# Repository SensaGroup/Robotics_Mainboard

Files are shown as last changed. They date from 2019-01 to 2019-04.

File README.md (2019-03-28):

# SENSA - Robotics_Mainboard

SENSA Mainboard is used on the Eurobot 2019 competition.

## Description
The Mainboard is the commander of the robot system. 
We used an Arduino Mega for the base and we developed the extension board

## Features
- 5V/12V inputs with protection
- 4x servo pinouts with external 5V power supply
- 6x 12V pneumatic valve controller
- 2x high-current relays 
- AX-12 support
- 6x optoisolated 12V infrared sensor inputs
- 6x binary 5V sensor inputs
- CAN-Bus (MCP25625)
- NRF24L01
- HC-05 Bluetooth pinout
- I2C/UART pinouts

## Software
All software is written in C for AVR.
View README in the Software folder.

## Pictures
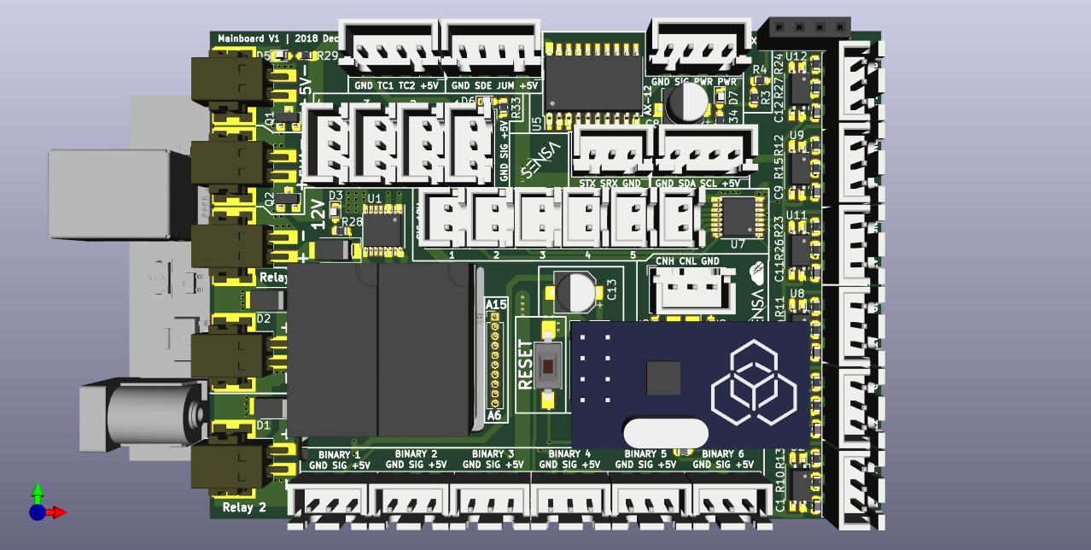
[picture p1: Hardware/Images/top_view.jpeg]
Top_view


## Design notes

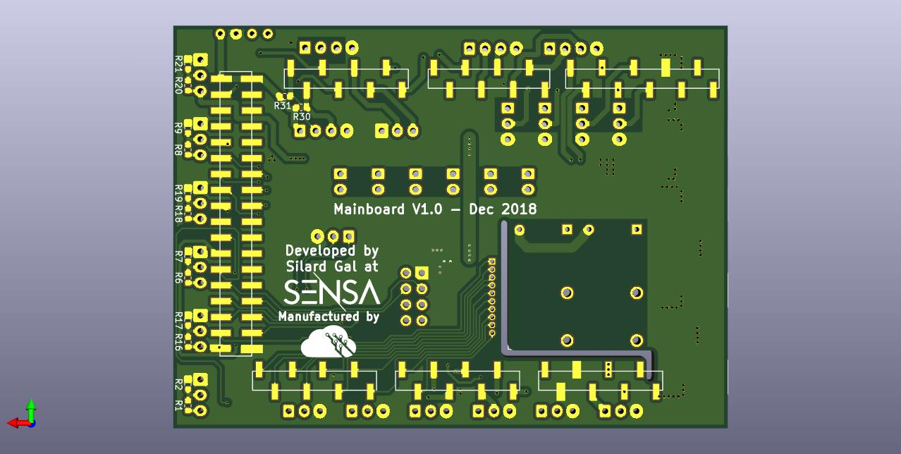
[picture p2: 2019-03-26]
Hardware/Images/bottom_view.jpeg

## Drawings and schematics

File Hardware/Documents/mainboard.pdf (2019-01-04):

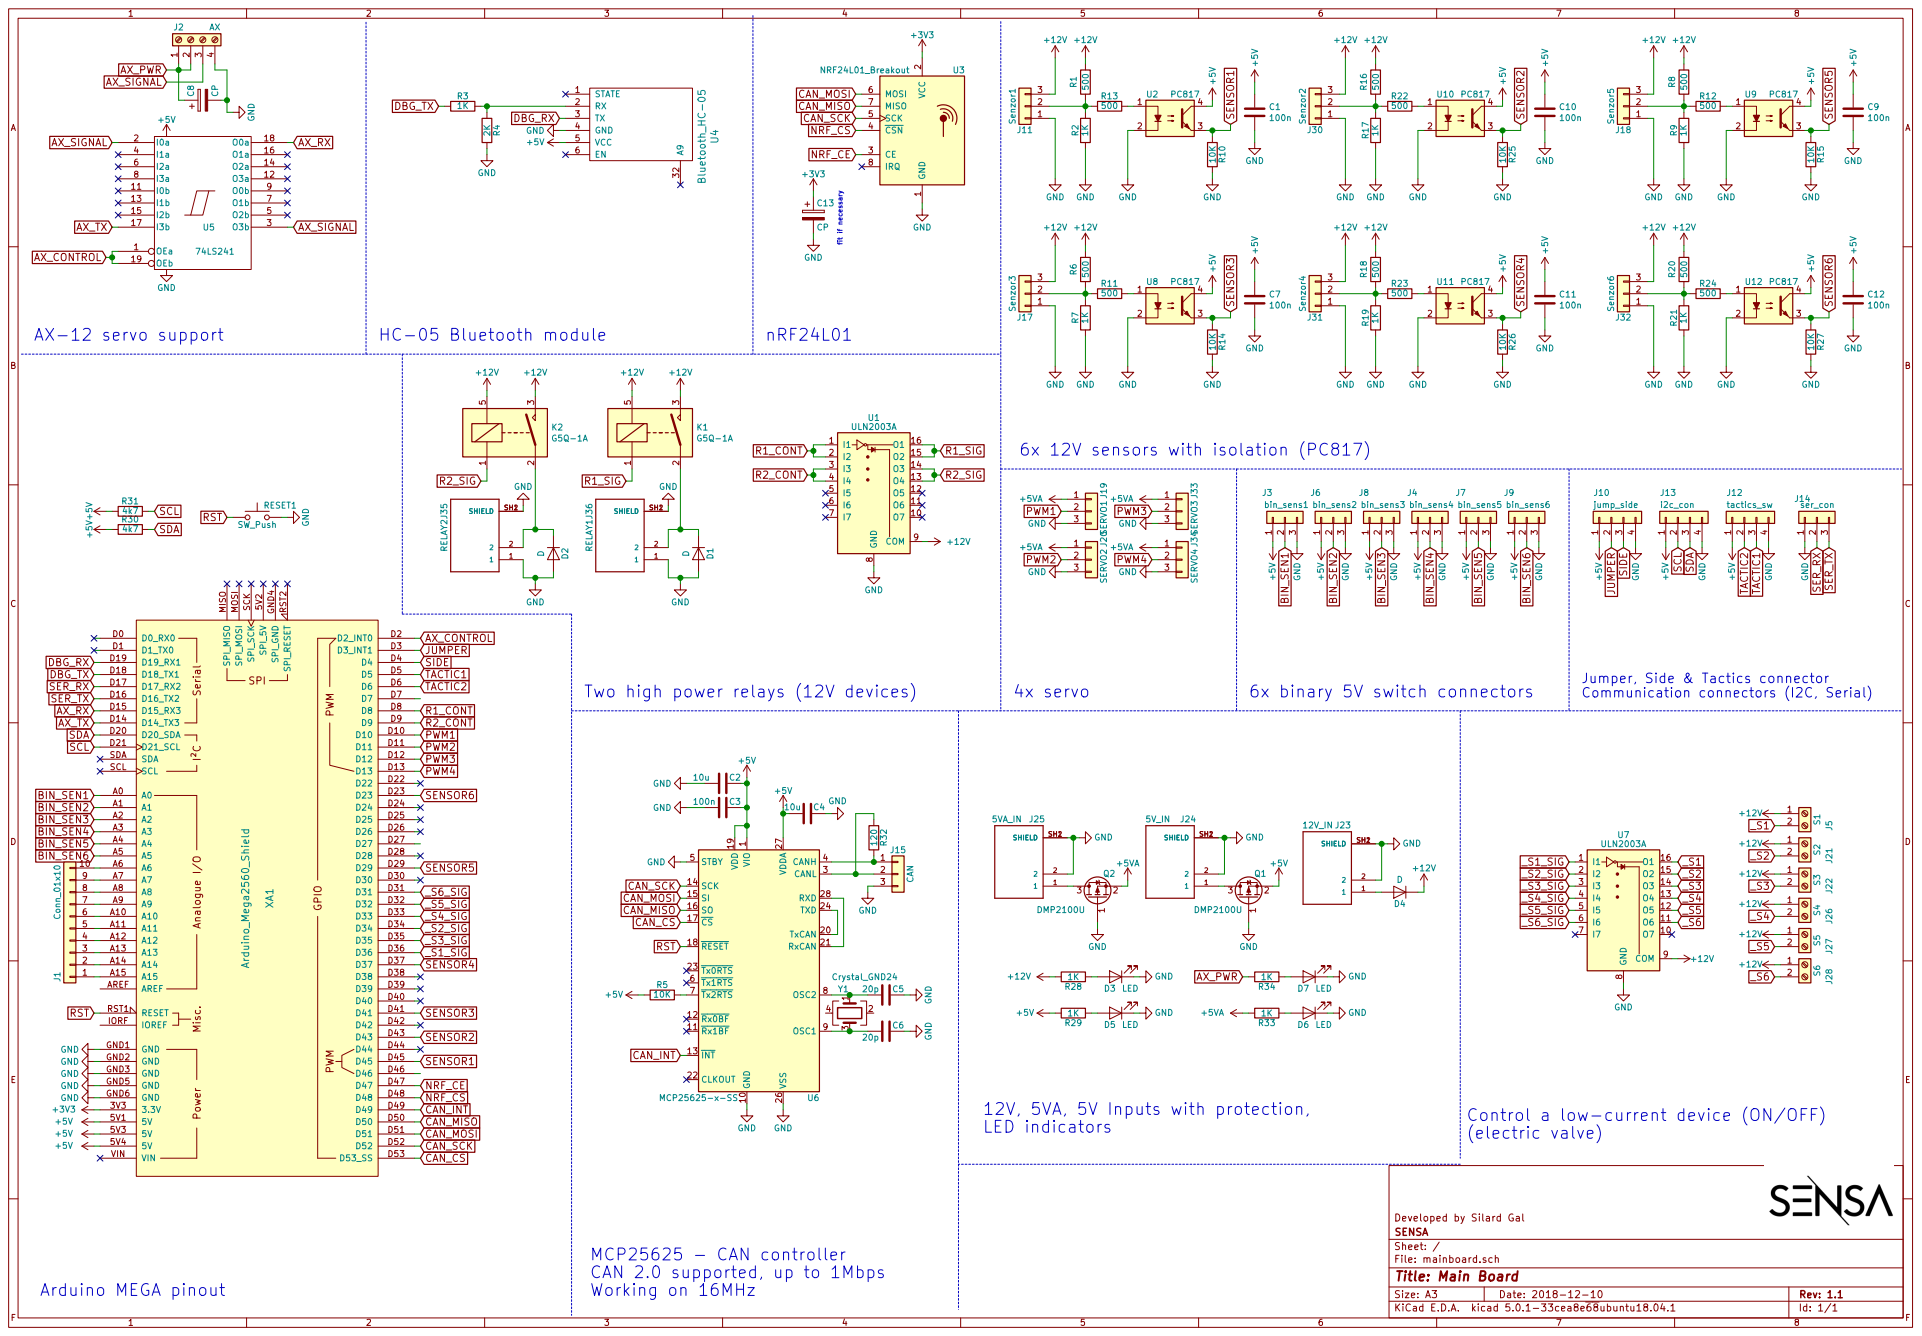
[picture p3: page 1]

2 CE 3 CSN 4 SCK 5 MOSI 6 MISO 7

Jumper, Side & Tactics connector
Communication connectors (I2C, Serial)

GND GND GND GND GND

Control a low-current device (ON/OFF)
(electric valve)

File: mainboard.sch Sheet: / SENSA

MCP25625 - CAN controller
CAN 2.0 supported, up to 1Mbps

Id: 1/1 Title: Main Board

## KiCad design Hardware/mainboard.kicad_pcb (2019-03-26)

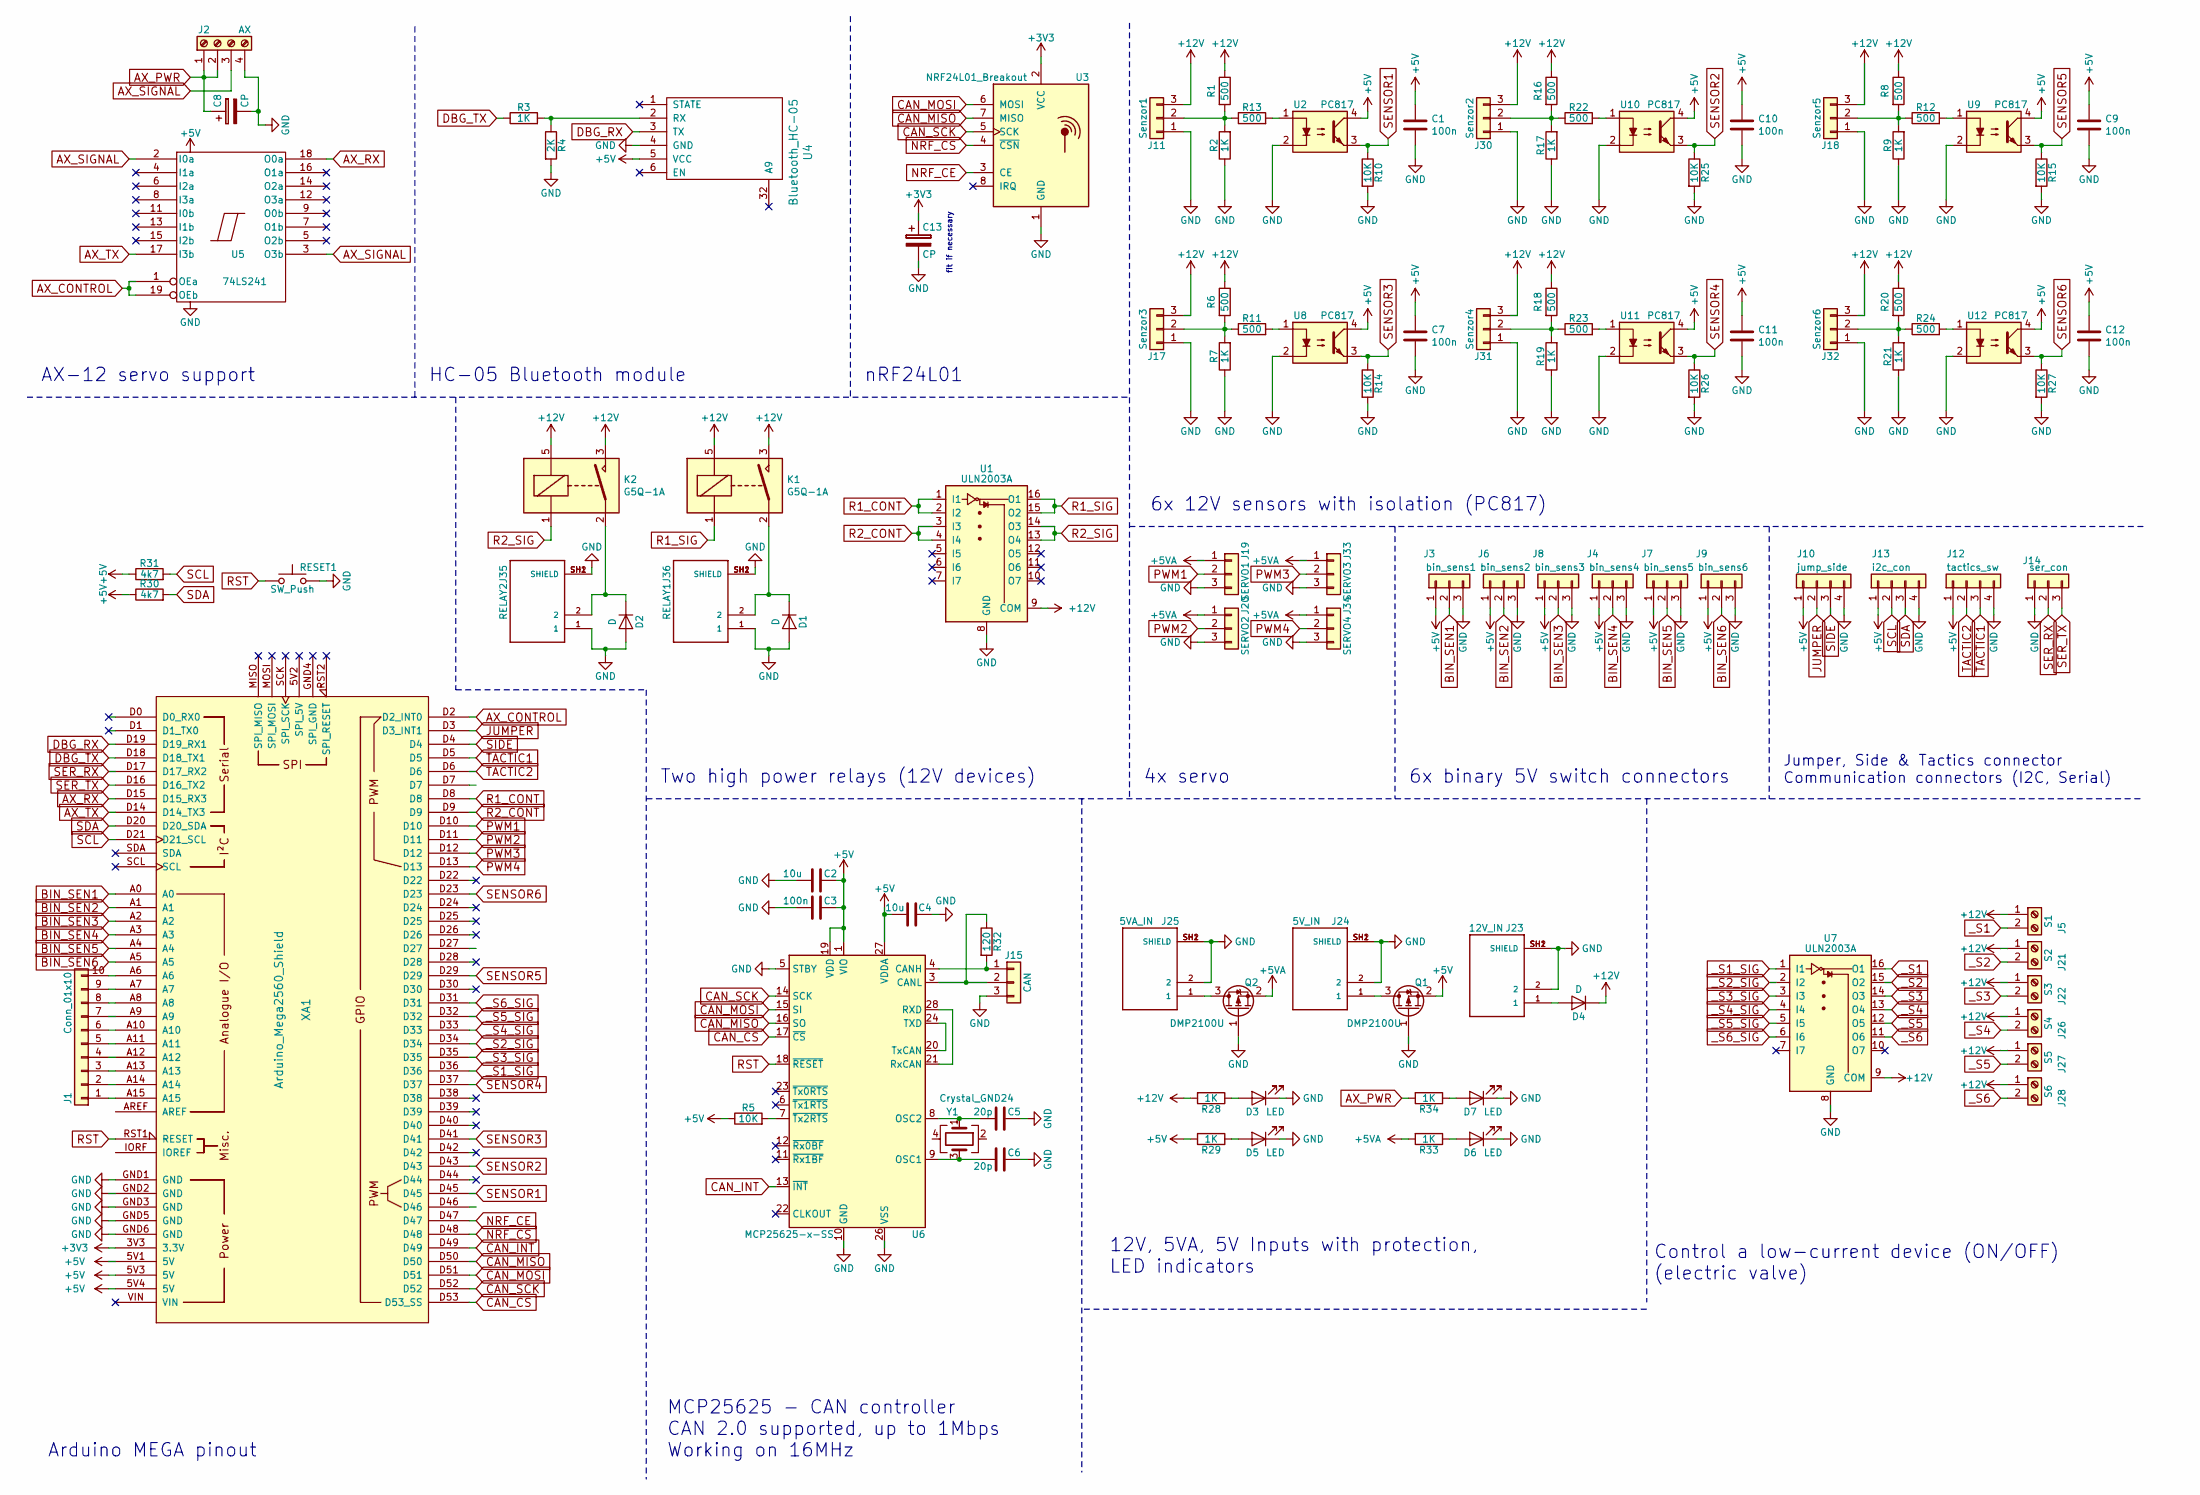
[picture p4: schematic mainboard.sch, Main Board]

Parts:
C1, C3, C7, C9, C10, C11, C12: 100n; C_0603_1608Metric
C2, C4: 10u; C_0603_1608Metric
C5, C6: 20p; C_0603_1608Metric
C8, C13: CP; CP_Elec_5x5.8
D1, D2, D4: D; D_SMA
D3, D5, D6, D7: LED; LED_0603_1608Metric
J1: Conn_01x10; PinHeader_1x10_P1.27mm_Vertical
J2: AX; JST_XH_B04B-XH-A_1x04_P2.50mm_Vertical
J3: bin_sens1; JST_XH_B03B-XH-A_1x03_P2.50mm_Vertical
J4: bin_sens4; JST_XH_B03B-XH-A_1x03_P2.50mm_Vertical
J5: S1; JST_XH_B02B-XH-A_1x02_P2.50mm_Vertical
J6: bin_sens2; JST_XH_B03B-XH-A_1x03_P2.50mm_Vertical
J7: bin_sens5; JST_XH_B03B-XH-A_1x03_P2.50mm_Vertical
J8: bin_sens3; JST_XH_B03B-XH-A_1x03_P2.50mm_Vertical
J9: bin_sens6; JST_XH_B03B-XH-A_1x03_P2.50mm_Vertical
J10: jump_side; JST_XH_B04B-XH-A_1x04_P2.50mm_Vertical
J11: Senzor1; JST_XH_B03B-XH-A_1x03_P2.50mm_Vertical
J12: tactics_sw; JST_XH_B04B-XH-A_1x04_P2.50mm_Vertical
J13: i2c_con; JST_XH_B04B-XH-A_1x04_P2.50mm_Vertical
J14: ser_con; JST_XH_B03B-XH-A_1x03_P2.50mm_Vertical
J15: CAN; JST_XH_B03B-XH-A_1x03_P2.50mm_Vertical
J17: Senzor3; JST_XH_B03B-XH-A_1x03_P2.50mm_Vertical
J18: Senzor5; JST_XH_B03B-XH-A_1x03_P2.50mm_Vertical
J19: SERVO1; JST_XH_B03B-XH-A_1x03_P2.50mm_Vertical
J20: SERVO2; JST_XH_B03B-XH-A_1x03_P2.50mm_Vertical
J21: S2; JST_XH_B02B-XH-A_1x02_P2.50mm_Vertical
J22: S3; JST_XH_B02B-XH-A_1x02_P2.50mm_Vertical
J23: 12V_IN; PHOENIX_1702473
J24: 5V_IN; PHOENIX_1702473
J25: 5VA_IN; PHOENIX_1702473
J26: S4; JST_XH_B02B-XH-A_1x02_P2.50mm_Vertical
J27: S5; JST_XH_B02B-XH-A_1x02_P2.50mm_Vertical
J28: S6; JST_XH_B02B-XH-A_1x02_P2.50mm_Vertical
J30: Senzor2; JST_XH_B03B-XH-A_1x03_P2.50mm_Vertical
J31: Senzor4; JST_XH_B03B-XH-A_1x03_P2.50mm_Vertical
J32: Senzor6; JST_XH_B03B-XH-A_1x03_P2.50mm_Vertical
J33: SERVO3; JST_XH_B03B-XH-A_1x03_P2.50mm_Vertical
J34: SERVO4; JST_XH_B03B-XH-A_1x03_P2.50mm_Vertical
J35: RELAY2; PHOENIX_1702473
J36: RELAY1; PHOENIX_1702473
K1, K2: G5Q-1A; Relay_SPST_Omron-G5Q-1A
Q1, Q2: DMP2100U; SOT-23
R1, R6, R8, R11, R12, R13, R16, R18, R20, R22, R23, R24: 500; R_0603_1608Metric
R2, R3, R7, R9, R17, R19, R21, R28, R29, R33, R34: 1K; R_0603_1608Metric
R4: 2K; R_0603_1608Metric
R5, R10, R14, R15, R25, R26, R27: 10K; R_0603_1608Metric
R30, R31: 4k7; R_0603_1608Metric
R32: 120; R_0603_1608Metric
RESET1: SW_Push; SW_SPST_FSMSM
U1, U7: ULN2003A; TSSOP-16-1EP_4.4x5mm_P0.65mm
U2, U8, U9, U10, U11, U12: PC817; SOP-4_4.4x2.8mm_P1.27mm
U3: NRF24L01_Breakout; PinHeader_2x04_P2.54mm_Vertical
U4: Bluetooth_HC-05
U5: 74LS241; SOIC-20W_7.5x12.8mm_P1.27mm
U6: MCP25625-x-SS; SSOP-28_5.3x10.2mm_P0.65mm
XA1: Arduino_Mega2560_Shield
Y1: Crystal_GND24; Crystal_SMD_SeikoEpson_FA238V-4Pin_3.2x2.5mm_HandSoldering

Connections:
+3V3: C13.1, U3.2 (VCC), XA1.3V3 (3.3V); also elsewhere on the board
+5V: C1.1, C2.1, C3.1, C4.1, C7.1, C9.1, C10.1, C11.1, C12.1, J3.1, J4.1, J6.1, J7.1, J8.1, J9.1, J10.1, J12.1, J13.1, Q1.2 (S), R5.1, R29.2, R30.1, R31.1, U2.4, U4.5 (VCC), U5.20 (VCC), U6.1 (VIO), U6.19 (VDD), U6.27 (VDDA), U8.4, U9.4, U10.4, U11.4, U12.4, XA1.5V1 (5V), XA1.5V3 (5V), XA1.5V4 (5V); also elsewhere on the board
+5VA: J19.1, J20.1, J33.1, J34.1, Q2.2 (S), R33.2
+12V: D4.1 (K), J5.1, J11.3, J17.3, J18.3, J21.1, J22.1, J26.1, J27.1, J28.1, J30.3, J31.3, J32.3, K1.3, K1.5, K2.3, K2.5, R1.1, R6.1, R8.1, R16.1, R18.1, R20.1, R28.2, U1.9 (COM), U7.9 (COM)
AX_CONTROL: U5.1 (OEa), U5.19 (OEb), XA1.D2 (D2_INT0); also elsewhere on the board
AX_PWR: C8.1, J2.1, J2.2, R34.2
AX_RX: U5.18 (O0a), XA1.D15 (D15_RX3); also elsewhere on the board
AX_SIGNAL: J2.3, U5.2 (I0a), U5.3 (O3b)
AX_TX: U5.17 (I3b), XA1.D14 (D14_TX3); also elsewhere on the board
BIN_SEN1: J3.2, XA1.A0; also elsewhere on the board
BIN_SEN2: J6.2, XA1.A1; also elsewhere on the board
BIN_SEN3: J8.2, XA1.A2; also elsewhere on the board
BIN_SEN4: J4.2, XA1.A3; also elsewhere on the board
BIN_SEN5: J7.2, XA1.A4; also elsewhere on the board
BIN_SEN6: J9.2, XA1.A5; also elsewhere on the board
CAN_CS: U6.17 (~CS), XA1.D53 (D53_SS); also elsewhere on the board
CAN_INT: U6.13 (~INT), XA1.D49; also elsewhere on the board
CAN_MISO: U3.7 (MISO), U6.16 (SO), XA1.D50; also elsewhere on the board
CAN_MOSI: U3.6 (MOSI), U6.15 (SI), XA1.D51; also elsewhere on the board
CAN_SCK: U3.5 (SCK), U6.14 (SCK), XA1.D52; also elsewhere on the board
DBG_RX: U4.3 (TX), XA1.D19 (D19_RX1); also elsewhere on the board
DBG_TX: R3.1, XA1.D18 (D18_TX1); also elsewhere on the board
GND: C1.2, C2.2, C3.2, C4.2, C5.1, C6.1, C7.2, C8.2, C9.2, C10.2, C11.2, C12.2, C13.2, D1.2 (A), D2.2 (A), D3.1 (K), D5.1 (K), D6.1 (K), D7.1 (K), J2.4, J3.3, J4.3, J6.3, J7.3, J8.3, J9.3, J10.4, J11.1, J12.4, J13.4, J14.1, J15.3, J17.1, J18.1, J19.3, J20.3, J23.2, J23.SH1 (SHIELD), J23.SH2 (SHIELD), J24.2, J24.SH1 (SHIELD), J24.SH2 (SHIELD), J25.2, J25.SH1 (SHIELD), J25.SH2 (SHIELD), J30.1, J31.1, J32.1, J33.3, J34.3, J35.1, J35.SH1 (SHIELD), J35.SH2 (SHIELD), J36.1, J36.SH1 (SHIELD), J36.SH2 (SHIELD), Q1.1 (G), Q2.1 (G), R2.1, R4.2, R7.1, R9.1, R10.2, R14.2, R15.2, R17.1, R19.1, R21.1, R25.2, R26.2, R27.2, RESET1.2, U1.8 (GND), U2.2, U3.1 (GND), U4.4 (GND), U5.10 (GND), U6.5 (STBY), U6.10 (GND), U6.26 (VSS), U7.8 (GND), U8.2, U9.2, U10.2, U11.2, U12.2, XA1.GND1 (GND), XA1.GND2 (GND), XA1.GND3 (GND), XA1.GND5 (GND), XA1.GND6 (GND); also elsewhere on the board
JUMPER: J10.2, XA1.D3 (D3_INT1); also elsewhere on the board
NRF_CE: U3.3 (CE), XA1.D47; also elsewhere on the board
NRF_CS: U3.4 (~CSN), XA1.D48; also elsewhere on the board
unnamed: C5.2, U6.8 (OSC2), Y1.1
unnamed: C6.2, U6.9 (OSC1), Y1.3
unnamed: D1.1 (K), J36.2, K1.2
unnamed: D2.1 (K), J35.2, K2.2
unnamed: D3.2 (A), R28.1
unnamed: D4.2 (A), J23.1
unnamed: D5.2 (A), R29.1
unnamed: D6.2 (A), R33.1
unnamed: D7.2 (A), R34.1
unnamed 35: J1.1, XA1.A15; also elsewhere on the board
unnamed 36: J1.2, XA1.A14; also elsewhere on the board
unnamed 37: J1.3, XA1.A13; also elsewhere on the board
unnamed 38: J1.4, XA1.A12; also elsewhere on the board
unnamed 39: J1.5, XA1.A11; also elsewhere on the board
unnamed 40: J1.6, XA1.A10; also elsewhere on the board
unnamed 41: J1.7, XA1.A9; also elsewhere on the board
unnamed 42: J1.8, XA1.A8; also elsewhere on the board
unnamed 43: J1.9, XA1.A7; also elsewhere on the board
unnamed 44: J1.10, XA1.A6; also elsewhere on the board
unnamed: J11.2, R1.2, R2.2, R13.1
unnamed: J15.1, R32.2, U6.4 (CANH)
unnamed: J15.2, R32.1, U6.3 (CANL)
unnamed: J17.2, R6.2, R7.2, R11.1
unnamed: J18.2, R8.2, R9.2, R12.1
unnamed: J24.1, Q1.3 (D)
unnamed: J25.1, Q2.3 (D)
unnamed: J30.2, R16.2, R17.2, R22.1
unnamed: J31.2, R18.2, R19.2, R23.1
unnamed: J32.2, R20.2, R21.2, R24.1
unnamed: R3.2, R4.1, U4.2 (RX)
unnamed: R5.2, U6.7 (~Tx2RTS)
unnamed: R11.2, U8.1
unnamed: R12.2, U9.1
unnamed: R13.2, U2.1
unnamed: R22.2, U10.1
unnamed: R23.2, U11.1
unnamed: R24.2, U12.1
unnamed: U6.20 (TxCAN), U6.24 (TXD)
unnamed: U6.21 (RxCAN), U6.28 (RXD)
unnamed 93: XA1.AREF; also elsewhere on the board
unnamed 94: XA1.D0 (D0_RX0); also elsewhere on the board
unnamed 95: XA1.D1 (D1_TX0); also elsewhere on the board
unnamed 96: XA1.D7; also elsewhere on the board
unnamed 97: XA1.D22; also elsewhere on the board
unnamed 98: XA1.D24; also elsewhere on the board
unnamed 99: XA1.D25; also elsewhere on the board
unnamed 100: XA1.D26; also elsewhere on the board
unnamed 101: XA1.D27; also elsewhere on the board
unnamed 102: XA1.D28; also elsewhere on the board
unnamed 103: XA1.D30; also elsewhere on the board
unnamed 104: XA1.D38; also elsewhere on the board
unnamed 105: XA1.D39; also elsewhere on the board
unnamed 106: XA1.D40; also elsewhere on the board
unnamed 107: XA1.D42; also elsewhere on the board
unnamed 108: XA1.D44; also elsewhere on the board
unnamed 109: XA1.D46; also elsewhere on the board
unnamed 110: XA1.IORF (IOREF); also elsewhere on the board
unnamed 111: XA1.SCL; also elsewhere on the board
unnamed 112: XA1.SDA; also elsewhere on the board
unnamed 113: XA1.VIN; also elsewhere on the board
PWM1: J19.2, XA1.D10; also elsewhere on the board
PWM2: J20.2, XA1.D11; also elsewhere on the board
PWM3: J33.2, XA1.D12; also elsewhere on the board
PWM4: J34.2, XA1.D13; also elsewhere on the board
R1_CONT: U1.1 (I1), U1.2 (I2), XA1.D8; also elsewhere on the board
R1_SIG: K1.1, U1.15 (O2), U1.16 (O1)
R2_CONT: U1.3 (I3), U1.4 (I4), XA1.D9; also elsewhere on the board
R2_SIG: K2.1, U1.13 (O4), U1.14 (O3)
RST: RESET1.1, U6.18 (~RESET), XA1.RST1 (RESET); also elsewhere on the board
SCL: J13.2, R31.2, XA1.D21 (D21_SCL); also elsewhere on the board
SDA: J13.3, R30.2, XA1.D20 (D20_SDA); also elsewhere on the board
SENSOR1: R10.1, U2.3, XA1.D45; also elsewhere on the board
SENSOR2: R25.1, U10.3, XA1.D43; also elsewhere on the board
SENSOR3: R14.1, U8.3, XA1.D41; also elsewhere on the board
SENSOR4: R26.1, U11.3, XA1.D37; also elsewhere on the board
SENSOR5: R15.1, U9.3, XA1.D29; also elsewhere on the board
SENSOR6: R27.1, U12.3, XA1.D23; also elsewhere on the board
SER_RX: J14.2, XA1.D17 (D17_RX2); also elsewhere on the board
SER_TX: J14.3, XA1.D16 (D16_TX2); also elsewhere on the board
SIDE: J10.3, XA1.D4; also elsewhere on the board
TACTIC1: J12.3, XA1.D5; also elsewhere on the board
TACTIC2: J12.2, XA1.D6; also elsewhere on the board
_S1: J5.2, U7.16 (O1)
_S1_SIG: U7.1 (I1), XA1.D36; also elsewhere on the board
_S2: J21.2, U7.15 (O2)
_S2_SIG: U7.2 (I2), XA1.D34; also elsewhere on the board
_S3: J22.2, U7.14 (O3)
_S3_SIG: U7.3 (I3), XA1.D35; also elsewhere on the board
_S4: J26.2, U7.13 (O4)
_S4_SIG: U7.4 (I4), XA1.D33; also elsewhere on the board
_S5: J27.2, U7.12 (O5)
_S5_SIG: U7.5 (I5), XA1.D32; also elsewhere on the board
_S6: J28.2, U7.11 (O6)
_S6_SIG: U7.6 (I6), XA1.D31; also elsewhere on the board

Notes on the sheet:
Control a low-current device (ON/OFF) (electric valve)
12V, 5VA, 5V Inputs with protection, LED indicators
MCP25625 - CAN controller CAN 2.0 supported, up to 1Mbps Working on 16MHz
Arduino MEGA pinout
AX-12 servo support
HC-05 Bluetooth module
nRF24L01
fit if necessary
6x 12V sensors with isolation (PC817)
Two high power relays (12V devices)
4x servo
6x binary 5V switch connectors
Jumper, Side & Tactics connector Communication connectors (I2C, Serial)

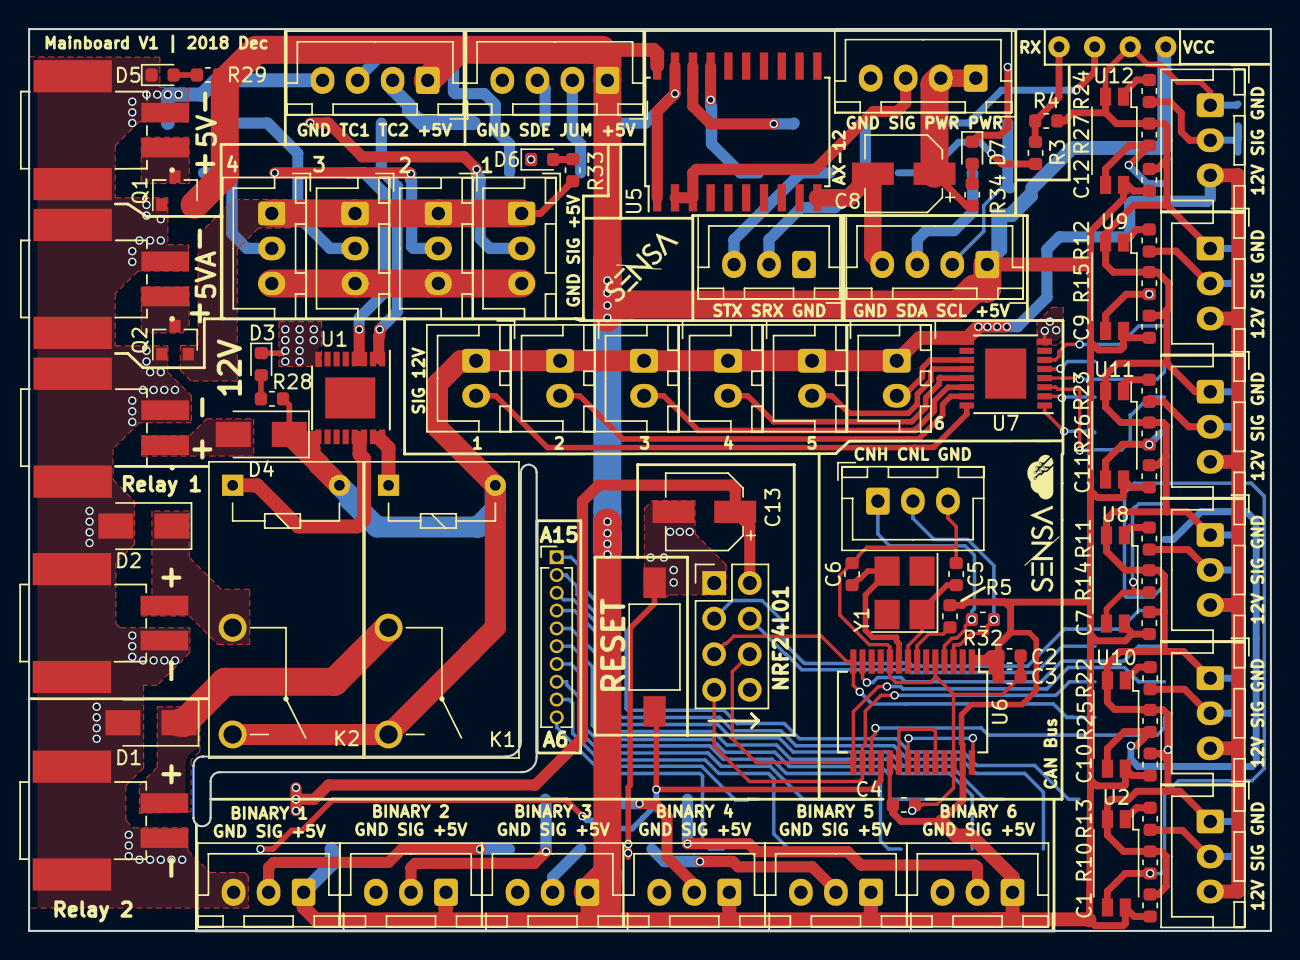
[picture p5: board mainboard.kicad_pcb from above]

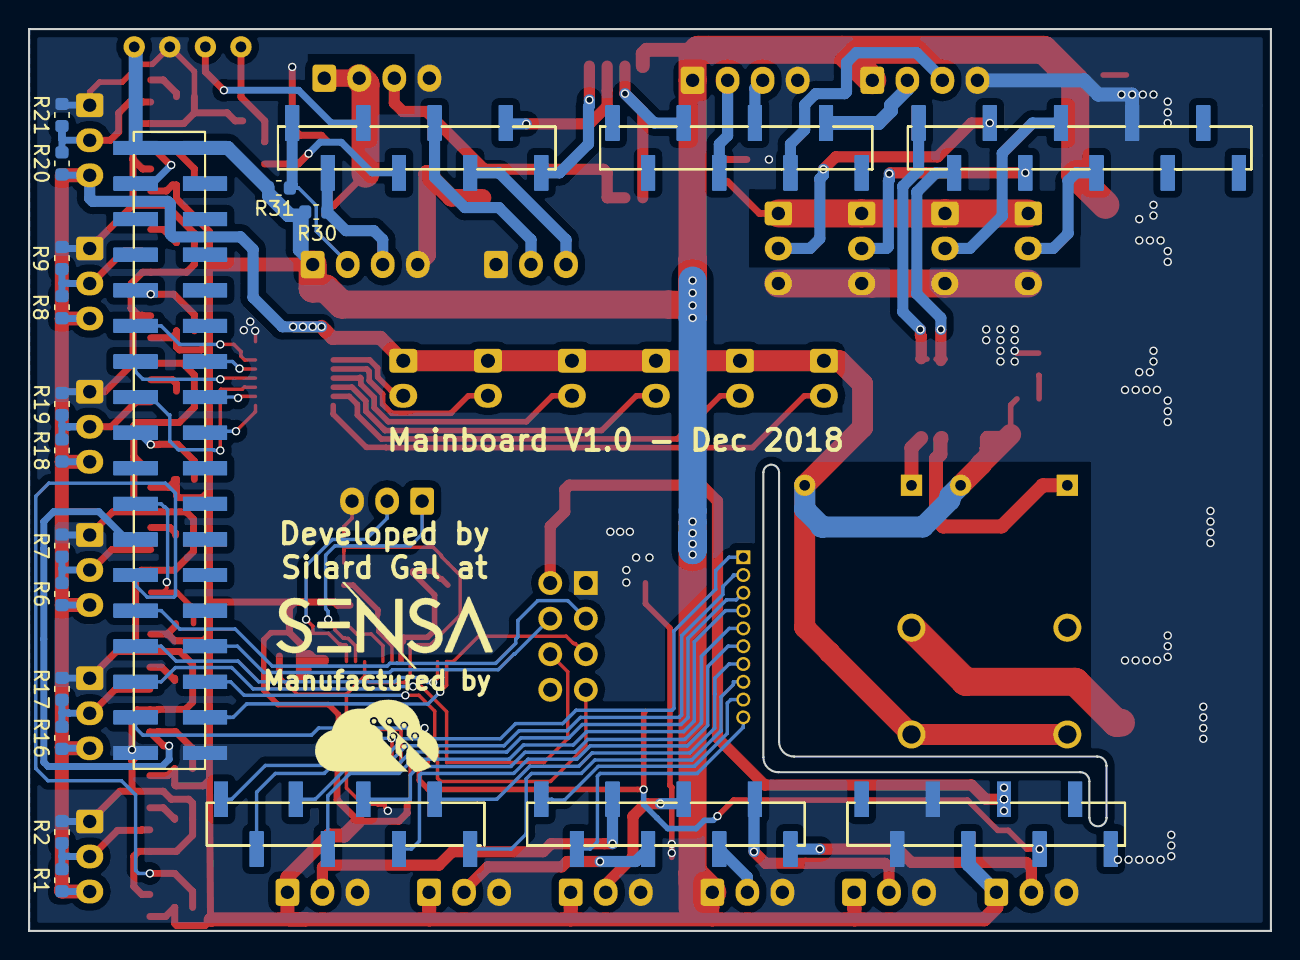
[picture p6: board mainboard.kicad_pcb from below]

Board: 2 copper layers, 88.6 x 64.4 mm, 108 parts (14 on the bottom side), 120 nets.

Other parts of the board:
XA1#2: Arduino_Mega2560_Shield

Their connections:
+3V3: XA1#2.3V3; also elsewhere on the board
+5V: XA1#2.5V1, XA1#2.5V3, XA1#2.5V4; also elsewhere on the board
AX_CONTROL: XA1#2.D2; also elsewhere on the board
AX_RX: XA1#2.D15; also elsewhere on the board
AX_TX: XA1#2.D14; also elsewhere on the board
BIN_SEN1: XA1#2.A0; also elsewhere on the board
BIN_SEN2: XA1#2.A1; also elsewhere on the board
BIN_SEN3: XA1#2.A2; also elsewhere on the board
BIN_SEN4: XA1#2.A3; also elsewhere on the board
BIN_SEN5: XA1#2.A4; also elsewhere on the board
BIN_SEN6: XA1#2.A5; also elsewhere on the board
CAN_CS: XA1#2.D53; also elsewhere on the board
CAN_INT: XA1#2.D49; also elsewhere on the board
CAN_MISO: XA1#2.D50; also elsewhere on the board
CAN_MOSI: XA1#2.D51; also elsewhere on the board
CAN_SCK: XA1#2.D52; also elsewhere on the board
DBG_RX: XA1#2.D19; also elsewhere on the board
DBG_TX: XA1#2.D18; also elsewhere on the board
GND: XA1#2.GND1, XA1#2.GND2, XA1#2.GND3, XA1#2.GND5, XA1#2.GND6; also elsewhere on the board
JUMPER: XA1#2.D3; also elsewhere on the board
NRF_CE: XA1#2.D47; also elsewhere on the board
NRF_CS: XA1#2.D48; also elsewhere on the board
unnamed 35: XA1#2.A15; also elsewhere on the board
unnamed 36: XA1#2.A14; also elsewhere on the board
unnamed 37: XA1#2.A13; also elsewhere on the board
unnamed 38: XA1#2.A12; also elsewhere on the board
unnamed 39: XA1#2.A11; also elsewhere on the board
unnamed 40: XA1#2.A10; also elsewhere on the board
unnamed 41: XA1#2.A9; also elsewhere on the board
unnamed 42: XA1#2.A8; also elsewhere on the board
unnamed 43: XA1#2.A7; also elsewhere on the board
unnamed 44: XA1#2.A6; also elsewhere on the board
unnamed 93: XA1#2.AREF; also elsewhere on the board
unnamed 94: XA1#2.D0; also elsewhere on the board
unnamed 95: XA1#2.D1; also elsewhere on the board
unnamed 96: XA1#2.D7; also elsewhere on the board
unnamed 97: XA1#2.D22; also elsewhere on the board
unnamed 98: XA1#2.D24; also elsewhere on the board
unnamed 99: XA1#2.D25; also elsewhere on the board
unnamed 100: XA1#2.D26; also elsewhere on the board
unnamed 101: XA1#2.D27; also elsewhere on the board
unnamed 102: XA1#2.D28; also elsewhere on the board
unnamed 103: XA1#2.D30; also elsewhere on the board
unnamed 104: XA1#2.D38; also elsewhere on the board
unnamed 105: XA1#2.D39; also elsewhere on the board
unnamed 106: XA1#2.D40; also elsewhere on the board
unnamed 107: XA1#2.D42; also elsewhere on the board
unnamed 108: XA1#2.D44; also elsewhere on the board
unnamed 109: XA1#2.D46; also elsewhere on the board
unnamed 110: XA1#2.IORF; also elsewhere on the board
unnamed 111: XA1#2.SCL; also elsewhere on the board
unnamed 112: XA1#2.SDA; also elsewhere on the board
unnamed 113: XA1#2.VIN; also elsewhere on the board
PWM1: XA1#2.D10; also elsewhere on the board
PWM2: XA1#2.D11; also elsewhere on the board
PWM3: XA1#2.D12; also elsewhere on the board
PWM4: XA1#2.D13; also elsewhere on the board
R1_CONT: XA1#2.D8; also elsewhere on the board
R2_CONT: XA1#2.D9; also elsewhere on the board
RST: XA1#2.RST1; also elsewhere on the board
SCL: XA1#2.D21; also elsewhere on the board
SDA: XA1#2.D20; also elsewhere on the board
SENSOR1: XA1#2.D45; also elsewhere on the board
SENSOR2: XA1#2.D43; also elsewhere on the board
SENSOR3: XA1#2.D41; also elsewhere on the board
SENSOR4: XA1#2.D37; also elsewhere on the board
SENSOR5: XA1#2.D29; also elsewhere on the board
SENSOR6: XA1#2.D23; also elsewhere on the board
SER_RX: XA1#2.D17; also elsewhere on the board
SER_TX: XA1#2.D16; also elsewhere on the board
SIDE: XA1#2.D4; also elsewhere on the board
TACTIC1: XA1#2.D5; also elsewhere on the board
TACTIC2: XA1#2.D6; also elsewhere on the board
_S1_SIG: XA1#2.D36; also elsewhere on the board
_S2_SIG: XA1#2.D34; also elsewhere on the board
_S3_SIG: XA1#2.D35; also elsewhere on the board
_S4_SIG: XA1#2.D33; also elsewhere on the board
_S5_SIG: XA1#2.D32; also elsewhere on the board
_S6_SIG: XA1#2.D31; also elsewhere on the board

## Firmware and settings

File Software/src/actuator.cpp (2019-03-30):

#include "actuator.h"
#include "mechanism.h"

Servo servo_1;  uint8_t servo1_current;
Servo servo_2;  uint8_t servo2_current;
Servo servo_3;  uint8_t servo3_current;
Servo servo_4;  uint8_t servo4_current;

uint8_t valve_pins[6]   = {36, 35, 34, 33, 32, 31};
uint8_t bin_pins[2]     = { A4, A5};
/*
 servo_1.write(0);
    delay(1000);
    servo_1.write(180);
    */

void move_servo_1(int pos) {
    servo_1.write(pos);
}
void move_servo_2(int pos) {
    servo_2.write(pos);
}
void move_servo_3(int pos) {
    servo_3.write(pos);
}
void move_servo_4(int pos) {
    servo_4.write(pos);
}

/*
 * Function:    bool init_actuator(void)
 * Description: init all actuators + can bus board
 */
bool init_actuator(void) {

    // setup main board relays
    pinMode(RELAY1_PIN, OUTPUT); digitalWrite(RELAY1_PIN, LOW);
    pinMode(RELAY2_PIN, OUTPUT); digitalWrite(RELAY2_PIN, LOW);

    // attach all servos
    servo_1.attach(10); servo_2.attach(11); servo_3.attach(12); servo_4.attach(13);
    move_servo_1(0);
    delay(1000);
    move_servo_1(180);
    
    // setup inputs and valve connectors
    for(int i=0; i<6; i++) {
        pinMode(valve_pins[i], OUTPUT);
        digitalWrite(valve_pins[i], LOW);

        pinMode(bin_pins[i], INPUT);
    }

    pinMode(A0, OUTPUT);    // dir right
    pinMode(A1, OUTPUT);    // step right
    pinMode(A2, OUTPUT);    // dir left
    pinMode(A3, OUTPUT);    // step left

    // setup the actuator board
    byte ping_data[8] = {'P', 1, 0, 0, 0, 0, 0, 0};

    can_send(ACTUATOR_CAN_ID, ping_data);

    if(can_wait_for_finish() == 0xff) {
        return true;
    } else {
        return false;
    }
} // end of init_actuator(...)

/*
 * Function:        uint8_t actuator_relay_toggle(byte num)
 * Description:     toggle the relay
 * Parameters:      byte num    - which relay
 */
uint8_t actuator_relay_toggle(byte num) {

    byte using_pin;

    if(num == 1) {
        using_pin = RELAY1_PIN;
    } else {
        using_pin = RELAY2_PIN;
    }

    digitalWrite(using_pin, !digitalRead(using_pin));

    return 0;

} // end of actuator_relay_toggle(...)

/*
 * Function:        uint8_t actuator_update_servo(byte num, uint8_t pos) 
 * Description:     update the servos
 * Parameters:      byte num    - which servo
 *                  uint8_t pos - the position
 */
uint8_t actuator_update_servo(int num, int pos) {

    switch(num) {
        case 1:
            servo_1.write(pos);
            break;
        case 2:
            servo_2.write(pos);
            break;
        case 3:
            servo_3.write(pos);
            break;
        case 4:
            servo_4.write(pos);
            break;
    }

    return 0;

} // end of actuator_update_servo(...)

/*
 * Function:        uint8_t actuator_update_valves(uint8_t num, uint8_t status)
 * Description:     update the valves
 * Parameters:      uint8_t num         - which conn/valve
 *                  uint8_t status      - ON/OFF
 */
uint8_t actuator_update_valves(uint8_t num, uint8_t status) {
    digitalWrite(valve_pins[num-1], status);
} // end of actuator_update_valves(...)

/*
 * Function:        uint8_t actuator_read_bin(uint8_t num)
 * Description:     read the binary sensors
 * Parameters:      uint8_t num         - which binary sensor
 */
uint8_t actuator_read_bin(uint8_t num) {
    return digitalRead(bin_pins[num-1]);
} // end of actuator_read_bin(...)

/*
 * Function:        uint8_t actuator_read_switch(uint8_t _switch)
 * Description:     read the switches from the actuator board
 */
uint8_t actuator_read_switch(uint8_t _switch) {

    // 1 - 8
    byte switch_data[8] = {'S', _switch, 0, 0, 0, 0, 0, 0};

    can_send(ACTUATOR_CAN_ID, switch_data);
    return can_wait_for_finish();

} // end of actuator_read_switch(...)

/*
 * Function:        uint8_t actuator_move_hbridge(int a, int b, byte num)
 * Description:     start the hbridge
 * Parameters:      int a       - pwm on A channel
 *                  int b       - pwm on B channel
 *                  byte num    - which motor
 */
uint8_t actuator_move_hbridge(int a, int b, byte num) {

    byte hbridge_data[8] = {'H', 'M', (byte)(a >> 8), (byte)(a & 0xFF), (byte)(b >> 8), (byte)(b & 0xFF), num};

    can_send(ACTUATOR_CAN_ID, hbridge_data);
    return can_wait_for_finish();

} // end of actuator_move_hbridge(...)

/* 
 * Function:        uint8_t actuator_break_hbridge(byte num)
 * Description:     break the motor on hbridge
 * Parameters:      byte num        - which motor
 */
uint8_t actuator_break_hbridge(byte num) {

    byte hbridge_data[8] = {'H','B', num, 0, 0, 0, 0, 0};

    can_send(ACTUATOR_CAN_ID, hbridge_data);
    return can_wait_for_finish();

} // end of actuator_break_hbridge(...)

/* 
 * Function:        uint8_t actuator_hbridge_timed(int dir, int achieve, int time, byte num)
 * Description:     time the hbridge 
 * Parameters:      int dir         - direction
 *                  int achieve     - the achievement
 *                  byte num        - the motor
 */
uint8_t actuator_hbridge_timed(int dir, int achieve, int time, byte num) {
    
    byte _num;
    
    if(num == 0) { _num = 'T'; } else { _num = 't'; }

    byte hbridge_data[8] = {'H', _num, (byte)(dir >> 8), (byte)(dir & 0xFF), (byte)(achieve >> 8), (byte)(achieve & 0xFF), (byte)(time >> 8), (byte)(time & 0xFF)};

    can_send(ACTUATOR_CAN_ID, hbridge_data);
    return can_wait_for_finish();

} // end of actuator_hbridge_timed(...)

/* 
 * Function:        uint8_t actuator_stepper_enable(byte status, byte num)
 * Description:     enable stepper
 * Parameters:      byte status - enable/disable
 *                  byte num    - which stepper
 */
uint8_t actuator_stepper_enable(byte status, byte num) {

    byte stepper_data[8] = {'s', 'E', status, num, 0, 0, 0, 0}; 

    can_send(ACTUATOR_CAN_ID, stepper_data);
    return can_wait_for_finish();

} // end of actuator_stepper_enable(...)

/* 
 * Function:        uint8_t actuator_stepper_rpm(int rpm, byte num) 
 * Description:     set the rpm 
 * Parameters:      int rpm     - setup the rpm
 *                  byte num    - which stepper
 */
uint8_t actuator_stepper_rpm(int rpm, byte num) {

    byte stepper_data[8] = {'s', 'R', (byte)(rpm >> 8), (byte)(rpm & 0xFF), num};

    can_send(ACTUATOR_CAN_ID, stepper_data);
    return can_wait_for_finish();

} // end of actuator_stepper_rpm(...)
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

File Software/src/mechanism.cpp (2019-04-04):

#include <Arduino.h>
#include "mechanism.h"

// STEPPER
void push_out_left(void) { 
    actuator_stepper_move(PACK_STEPS, STEPPER_FORWARD, SCP_LEFT_STEPPER_ID);
}

void pull_back_left(void) {
    actuator_stepper_move(PACK_STEPS, STEPPER_BACKWARD, SCP_LEFT_STEPPER_ID);
}

void push_out_right(void) { 
    actuator_stepper_move(PACK_STEPS, STEPPER_FORWARD, SCP_RIGHT_STEPPER_ID);
}

void pull_back_right(void) {
    actuator_stepper_move(PACK_STEPS, STEPPER_BACKWARD, SCP_RIGHT_STEPPER_ID);
}





// SERVOS
void servo_grab_left(void) {
   move_servo_1(SERVO_GRAB_LEFT_POS);
}

void servo_grab_right(void) {
    move_servo_1(SERVO_GRAB_RIGHT_POS);
}

void servo_grab(int side) {
    if(side == SCP_LEFT_STEPPER_ID) {
        servo_grab_left();
    } else if(side == SCP_RIGHT_STEPPER_ID) {
        servo_grab_right();
    }
} 


void servo_front_left_out() { move_servo_2(SERVO_FRONT_LEFT_OUT_POS); } void servo_front_left_in() { move_servo_2(SERVO_FRONT_LEFT_IN_POS); }
void servo_front_right_out() {  move_servo_3(SERVO_FRONT_RIGHT_OUT_POS); } void servo_front_right_in() { move_servo_2(SERVO_FRONT_RIGHT_IN_POS); }


// SWITCHES
uint8_t switch_front_left_servo()       { return actuator_read_bin(1); }
uint8_t switch_front_right_servo()      { return actuator_read_bin(2); }
uint8_t switch_front_left()             { return actuator_read_bin(3); }
uint8_t switch_front_right()            { return actuator_read_bin(4); }

uint8_t switch_lift_up()                { return actuator_read_bin(5); }
uint8_t switch_lift_center()            { return actuator_read_bin(6); }
uint8_t switch_lift_down()              { return actuator_read_bin(7); }

void lift_up() {
    actuator_move_hbridge(LIFT_SPEED, 0, 1);
    while(switch_lift_up() != LIFT_UP_DETECTED);
    actuator_break_hbridge(1);
}

void lift_down() {
    actuator_move_hbridge(0, LIFT_SPEED, 1);
    while(switch_lift_up() != LIFT_DOWN_DETECTED);
    actuator_break_hbridge(1);
}

void lift_center() {
    if(switch_lift_up() == LIFT_UP_DETECTED) {
        actuator_move_hbridge(0, LIFT_SPEED, 1);
    } else if(switch_lift_down() == LIFT_DOWN_DETECTED) {
        actuator_move_hbridge(LIFT_SPEED, 0, 1);
    }
    while(switch_lift_center() != LIFT_CENTER_DETECTED);
    actuator_break_hbridge(1);
}

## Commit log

2018-08-30 Beta version
    [mainboard.kicad_pcb, mainboard.sch]
2019-01-04 Finished version 1.0
    [mainboard-2018-10-16-12-17-26.sch, mainboard-2018-10-23-00-33-00.sch, mainboard-2018-10-25-20-59-39.sch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]
2019-03-26 Readme and images
    [mainboard.kicad_pcb, mainboard.sch]
2019-03-28 Hardware/Software folders
    [mainboard-2018-10-16-12-17-26.sch, mainboard-2018-10-23-00-33-00.sch, mainboard-2018-10-25-20-59-39.sch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]
2019-03-28 Added comments to lidar and sys
2019-03-28 Comments to actuator
2019-03-28 added comments to odometry
2019-03-30 Mechanisms, actuators, lidar and nrf sa;; seti[
